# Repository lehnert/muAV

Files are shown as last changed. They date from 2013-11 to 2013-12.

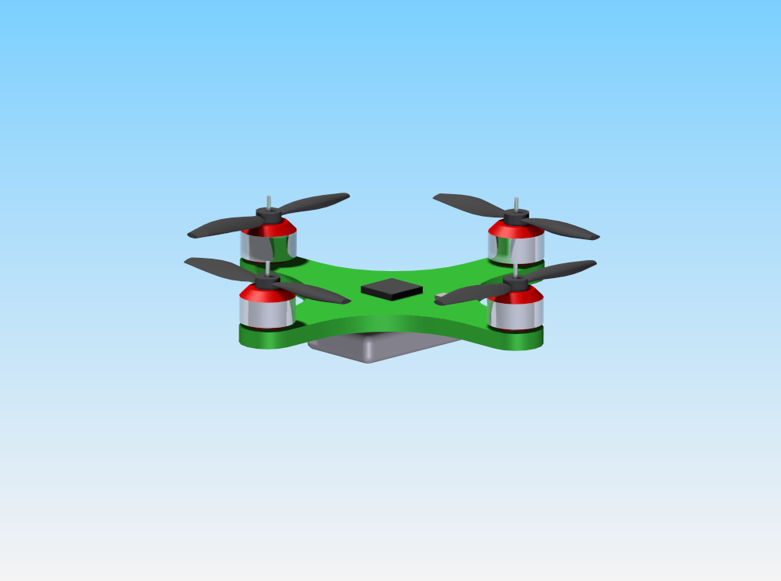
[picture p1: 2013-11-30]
Mechanial Design/images/quadrotor_image2.bmp

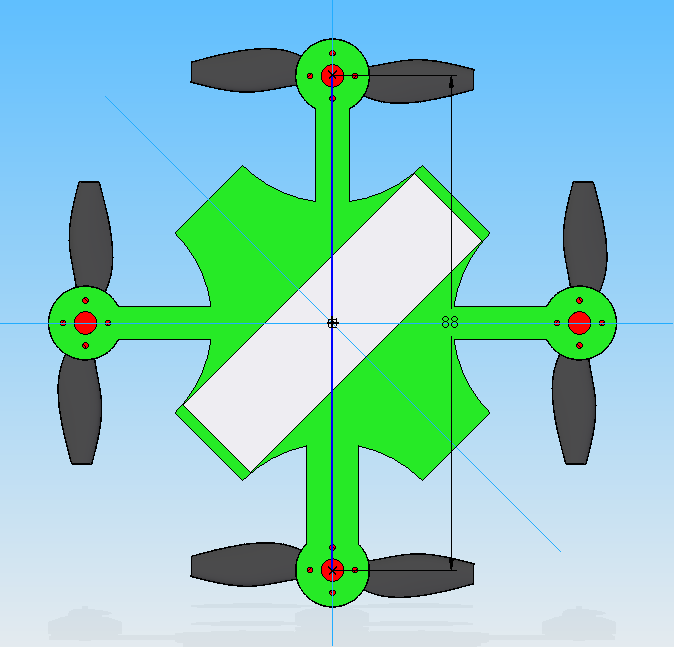
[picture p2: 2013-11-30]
Mechanial Design/images/quadrotor_image4_dimensions2.bmp

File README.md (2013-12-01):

µAV (muAV - Micro Unmanned Aerial Vehicle ) 
====

This project has been developed within the Cyphy Lab at the Queensland University of Technology. More information can be found at https://wiki.qut.edu.au/display/cyphy/Open+Source+Palm+Sized+Quadrotor

The aim of this project is to develop an open source micro unmanned aerial vehicle that is capable of autonomously nagivating within an indoor environment, which also fits in the palm of your hand. The concept has been designed to be cheap and easily constructed by using a single PCB board as the mechanical and electrical design of the system. An image of the final design is shown below.

Motivation:

The aim of the micro quadrotor project is to provide a lightweight (approximately 86g) and cheap robotic research platform that can be used for a range of robotic applications. One possible application could be a cheap test bed for robotic swarm research. This project was created to start an open source PCB only quadrotor for research applications. The idea was to create the simplest PCB only design in which all hardware is integrated. The hardware was selected to be state of the art allowing the system to be fully autonomous and used in high level research applications. Applications could include low cost robotic swarms or search and rescue in constrained environments.

Contributors:

Christophe Lehnert - https://wiki.qut.edu.au/display/cyphy/Chris+Lehnert
Peter Corke - https://wiki.qut.edu.au/display/cyphy/Peter+Corke

License:

 GNU GENERAL PUBLIC LICENSE  Version 3, 29 June 2007

 Copyright (C) 2007 Free Software Foundation, Inc. [http://fsf.org/]
 Everyone is permitted to copy and distribute verbatim copies
 of this license document, but changing it is not allowed.

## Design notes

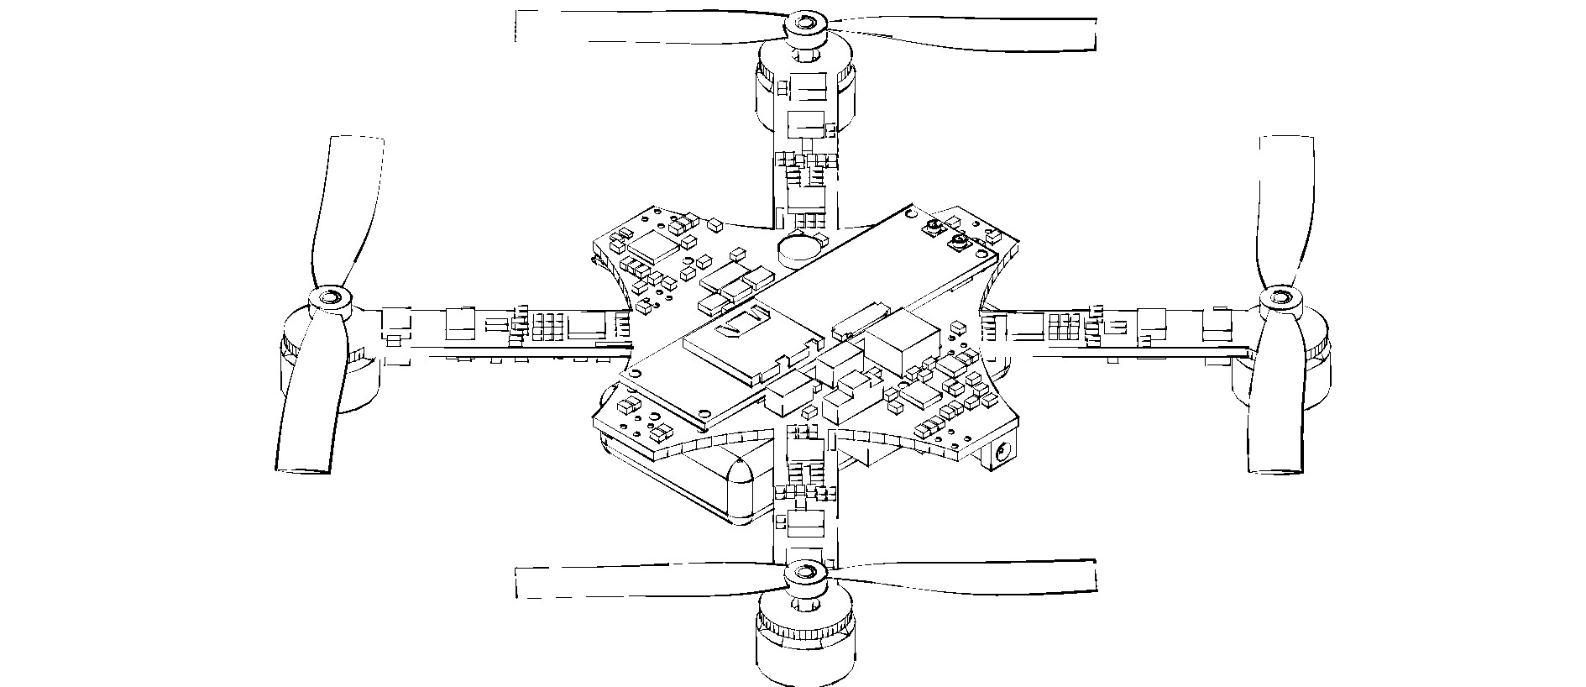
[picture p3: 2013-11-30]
Mechanial Design/images/quadrotor.jpg

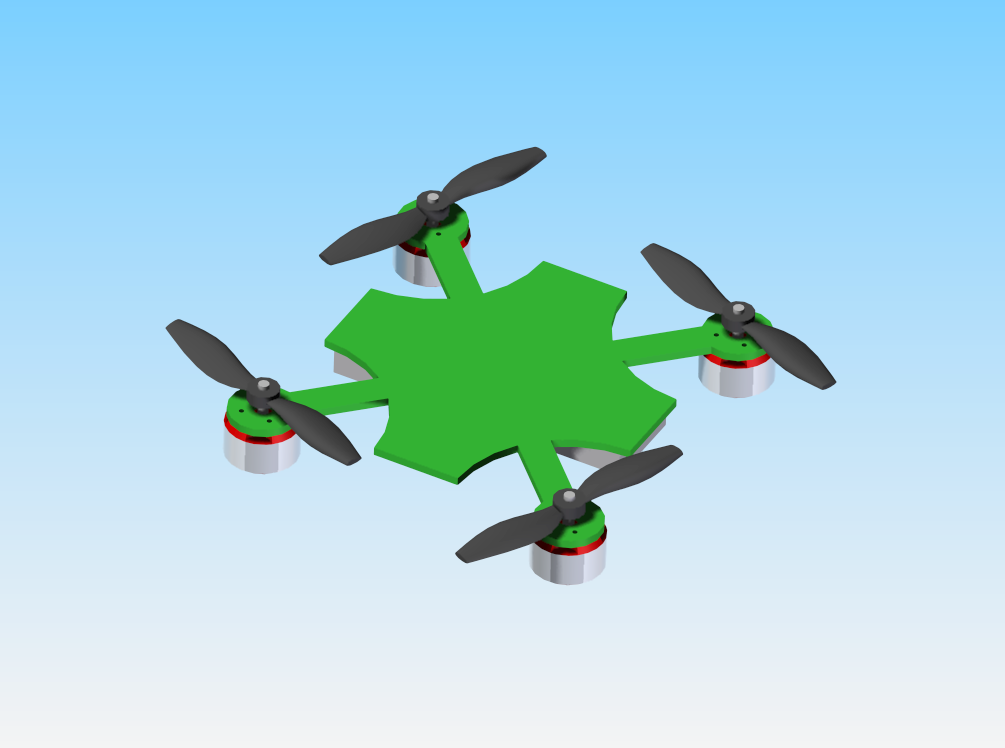
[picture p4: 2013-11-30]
Mechanial Design/images/new motor mounted.bmp

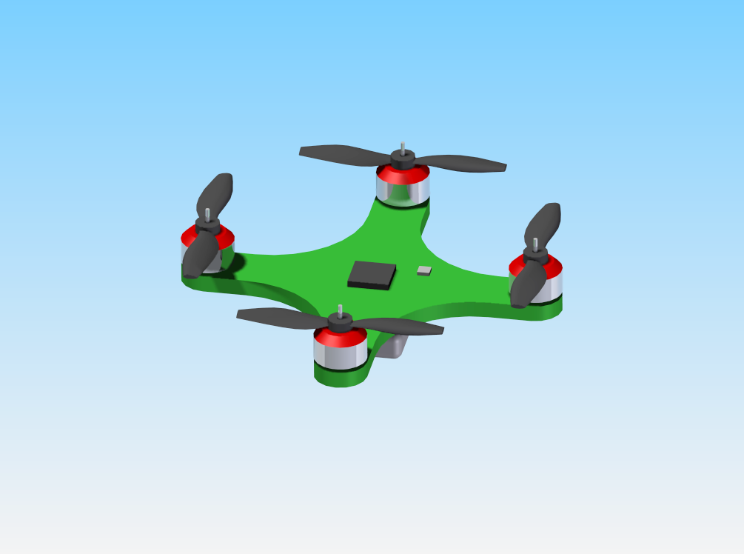
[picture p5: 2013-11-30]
Mechanial Design/images/quadrotor_image1.bmp

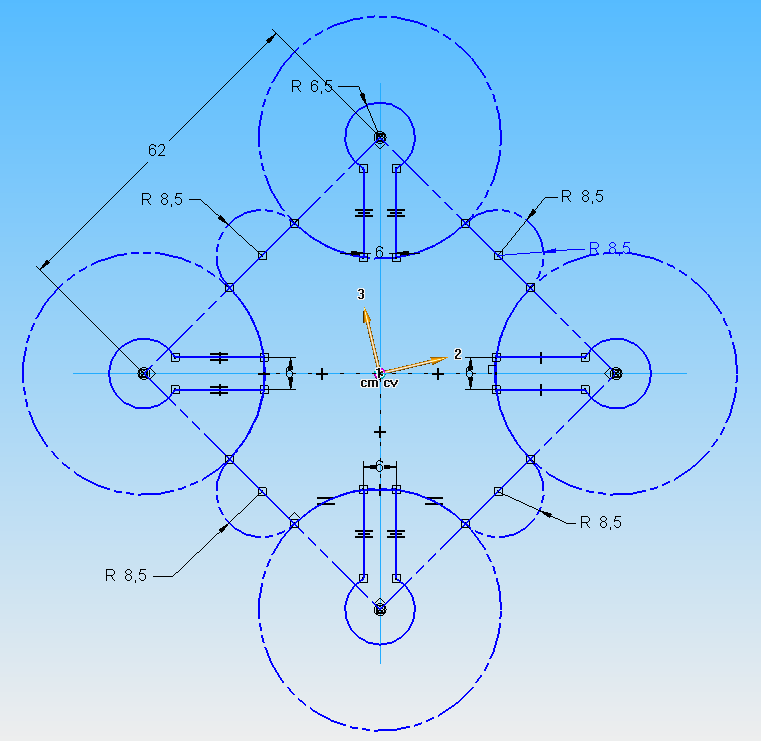
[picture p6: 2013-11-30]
Mechanial Design/images/quadrotor_image4_dimensions3.bmp

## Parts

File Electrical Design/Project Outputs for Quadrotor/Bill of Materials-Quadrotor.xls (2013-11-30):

Comment | Designator | Value | Footprint | Quantity | Manufacturer 1 | Supplier 1 | Supplier Order Qty 1 | Supplier Part Number 1 | Supplier Stock 1 | Supplier Subtotal 1 | Supplier Unit Price 1
HMC5843 | Mag1 |  | HMC5843 | 1 | Loading... | Sparkfun |  | COM-09441
SW-PB | SW1, SW2 |  | SM_SW | 2 | Loading... | Sparkfun |  | COM-08229
Triple axis gyroscope | IMU |  | QFN50P400X400X95-24N | 1 |  | Invensense
XTAL | XTAL |  | XTAL 16Mhz | 1 | Loading... | Farnell |  | 1640930
 | Rsns1 | 0.02 75PPM | CRA2512 | 1 | Bourns Inc. | Digi-Key | 1 | CRA2512-FZ-R020ELFCT-ND | 57343 | 0.49 | 0.49
3 axis accelerometer | ACCEL |  | 16 pin 3mmx3mm LGA | 1 | Analog Devices Inc | Digi-Key | 1 | ADXL345BCCZ-RLCT-ND | 12493 | 7.79 | 7.79
32Khz Oscillator | Osc2 |  | Oscillator | 1 | Abracon Corporation | Digi-Key | 1 | 535-9999-1-ND | 2117 | 5.06 | 5.06
ATmega8L-8AC | U1, uC1_E1, uC1_E2, uC1_E3, uC1_E4 |  | 32A_N | 5 | Atmel | Digi-Key | 5 | ATMEGA8L-8MU-ND, ATMEGA328-AU-ND
BC817-25 | Q1_E1, Q1_E2, Q1_E3, Q1_E4, Q2_E1, Q2_E2, Q2_E3, Q2_E4, Q3_E1, Q3_E2, Q3_E3, Q3_E4 |  | SOT-23 | 12 | NXP Semiconductors | Digi-Key | 12 | 568-1630-1-ND | 211012 | 2.59 | 0.22
BQ24103A | USBCHRG |  | QFN50P350X450X100-20N | 1 | Texas Instruments | Digi-Key | 1 | 296-22739-1-ND | 11380 | 6 | 6
Bq29312A | Bprot1 |  | TSOP65P640X120-24N | 1 | Texas Instruments | Digi-Key | 1 | 296-19870-1-ND | 874 | 3 | 3
CHOKE | FB2, FB3 |  | INDC1608L | 2 | Taiyo Yuden | Digi-Key | 2 | 587-1869-1-ND | 27225 | 0.66 | 0.33
Diode 10TQ035 | D14, D15 |  | DIODE | 2 | ON Semiconductor | Digi-Key | 2 | MBRS320T3GOSCT-ND | 17230 | 1.6 | 0.8
FDN-306P | Q4 |  | SOT-23 | 1 | Fairchild Semiconductor | Digi-Key | 1 | FDN306PCT-ND | 19874 | 0.55 | 0.55
IC_FT232RQ | FTDI |  | QFN-32 | 1 | FTDI, Future Technology Devices International Ltd | Digi-Key | 1 | 768-1067-2-ND | 0
Inductor | L1, L4 | 10uH, 15uH | INDM7575X45N | 2 | SUMIDA AMERICA COMPONENTS INC | Digi-Key | 2 | 308-1502-1-ND | 8486 | 2.84 | 1.42
MIC5427 | Reg1 |  | SOT23-STD-5-Lead | 1 | Micrel Inc | Digi-Key | 1 | 576-1288-1-ND | 10713 | 0.9 | 0.9
microUSB | mUSB1 |  | microUSB | 1 | Molex Inc | Digi-Key | 1 | WM17141CT-ND | 12801 | 1.31 | 1.31
MOSFET-N | Q8, Q10 |  | CSD16321Q5 | 2 | Texas Instruments | Digi-Key | 2 | 296-24517-1-ND | 9102 | 4.56 | 2.28
MOSFET-P | CHG1, DSG1, Q5, Q6, Q7 |  | CSD16321Q5_PFET | 5 | Texas Instruments | Digi-Key | 5 | 296-24260-1-ND | 14707 | 7.75 | 1.55
PWR2.5 | DC IN |  | DC Power JAck | 1 | CUI Inc | Digi-Key | 1 | CP1-022PJCT-ND | 3574 | 1.34 | 1.34
Rpull | Rsns2 | 0.1 | CRA2512 | 1 | Bourns Inc. | Digi-Key | 1 | CRA2512-FZ-R100ELFCT-ND | 33045 | 0.49 | 0.49
single tristate output line buffer | B1 |  | SOT95P280X145-5N | 1 | Texas Instruments | Digi-Key | 1 | 296-1115-1-ND | 12104 | 0.42 | 0.42
SW DPDT | S1 |  | SPDT | 1 | C&K Components | Digi-Key | 1 | 401-2002-1-ND | 14690 | 0.56 | 0.56
Switch mode regulator | 3.3PWR |  | TSOP65P640X120_HS-16N | 1 | Texas Instruments | Digi-Key | 1 | 296-22457-1-ND | 4016 | 10.34 | 10.34
T491A | C59 | 68uF | A | 1 | Kemet | Digi-Key | 1 | 399-4698-1-ND | 87013 | 0.88 | 0.88
T492C | C47_E1, C47_E2, C47_E3, C47_E4, C66 | 100uF | C | 5 | Kemet | Digi-Key | 5 | 399-5214-1-ND | 83455 | 6.7 | 1.34
Vtrans_2Bit | Vtrans1 |  | TSOP65P400X130-8N | 1 | Texas Instruments | Digi-Key | 1 | 296-17232-1-ND | 20290 | 0.84 | 0.84
 | C25, C61, C63, C64, C65 | 0.1uF, 10uF | 0603_CAP | 5
 | JP3, JP4, R52, R53, R54, R61, R62, R63 | 7.5K, 100 | 0603_RES | 8
 | R55, R56, R60 | 100K | RESC1608L | 3
2 Cell Battery | Battery |  | Turnigy Nanotech 2cell | 1
brushless motor | MTR1_E1, MTR1_E2, MTR1_E3, MTR1_E4 |  | Motor Combo | 4
Cap | C11, C12, C13, C14, C15, C16, C17, C18, C19, C20, C21, C22, C23 | 100nF, 100pF | 0603_CAP | 13
Cap Pol3 | C50, C52 | 1uF, 10uF | 0603_Cap | 2
Gumstix Overo Fire | GSTX1 |  | GUMSTIX | 1
Header 4 | P1, P2_E1, P2_E2, P2_E3, P2_E4 |  | PRG_HEADER | 5
JUMPER | JP1, JP2 |  | JUMPER | 2
LED0 | CHRG, DONE, LED1, LED2, LED_E1, LED_E2, LED_E3, LED_E4, PWR, PWR ON, RX1, TX1 |  | 0603_RES | 12
NP mosfet pair | NPA1_E1, NPA1_E2, NPA1_E3, NPA1_E4, NPB1_E1, NPB1_E2, NPB1_E3, NPB1_E4, NPC1_E1, NPC1_E2, NPC1_E3, NPC1_E4 |  | SOIC127P600-8L | 12
Rdrive | R6_E1, R6_E2, R6_E3, R6_E4, R11_E1, R11_E2, R11_E3, R11_E4 | 10K | 0603_RES | 8
Res Thermal | RT1 |  | RESC2012N | 1
Res1 | R27, R28, R29, R30, R31, R32, R33, R35, R36, R37, R38, R39, R40, R41, R42, R43, R44, R45, R46 | 1K | 0603_RES | 19
Res3 | R1, R2, R50, R51, R57, R58, R59 | 5.7K, 10K, 20K | 0603_RES | 7
Rpull | R3, R4_E1, R4_E2, R4_E3, R4_E4, R5_E1, R5_E2, R5_E3, R5_E4, R7_E1, R7_E2, R7_E3, R7_E4, R8_E1, R8_E2, R8_E3, R8_E4, R9_E1, R9_E2, R9_E3, R9_E4, R10_E1, R10_E2, R10_E3, R10_E4, R12_E1, R12_E2, R12_E3, R12_E4, R13_E1, R13_E2, R13_E3, R13_E4, R14_E1, R14_E2, R14_E3, R14_E4, R15_E1, R15_E2, R15_E3, R15_E4, R16_E1, R16_E2, R16_E3, R16_E4, R17_E1, R17_E2, R17_E3, R17_E4, R18_E1, R18_E2, R18_E3, R18_E4, R19_E1, R19_E2, R19_E3, R19_E4, R20_E1, R20_E2, R20_E3, R20_E4, R21_E1, R21_E2, R21_E3, R21_E4, R22_E1, R22_E2, R22_E3, R22_E4, R23_E1, R23_E2, R23_E3, R23_E4, R24_E1, R24_E2, R24_E3, R24_E4, R25_E1, R25_E2, R25_E3, R25_E4, R26_E1, R26_E2, R26_E3, R26_E4, R34_E1, R34_E2, R34_E3, R34_E4, R47, R48, R49, R64, R65, R66, R67_E1, R67_E2, R67_E3, R67_E4, R68_E1, R68_E2, R68_E3, R68_E4, R69_E1, R69_E2, R69_E3, R69_E4, R70_E1, R70_E2, R70_E3, R70_E4, R71, R72, R73, R74, R75, R76_E1, R76_E2, R76_E3, R76_E4, R77 | 1K, 4.7K, 8.2K, 9.31K, 10K, 16K, 33K, 100, 270, 442K | 0603_RES | 121
SCP1000-D11 | Prssr1 |  | SCP1000-D11 | 1
SDP8436 | SENS1, SENS2, SENS3, SENS4, SENS5, SENS6 |  | T-1SL | 6
SEP8736 | E1, E2, E3, E4, E5, E6 |  | T-1SL | 6
X7R Cap | C1, C2, C3, C4, C5, C6, C7, C8, C9, C10, C24, C26, C27, C28, C29, C30, C31, C32, C33, C34, C35, C36, C37, C38, C39, C40, C41, C42, C43, C44, C45_E1, C45_E2, C45_E3, C45_E4, C46, C48, C51, C53, C54, C55_E1, C55_E2, C55_E3, C55_E4, C56, C57, C58, C60, C62, Cesc1_E1, Cesc1_E2, Cesc1_E3, Cesc1_E4 | 0.1uF, 0.22uF, 0.47uF, 1uF, 2.2nF, 4.7uF, 10nF, 10uF | 0603_CAP | 52

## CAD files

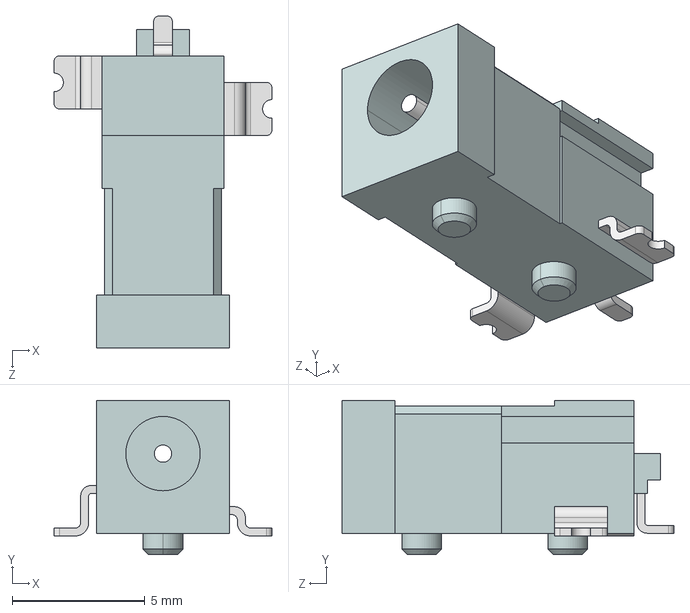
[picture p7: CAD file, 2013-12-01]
DataSheets/Other components/CUI-PJ1-022-SMT.step
8.20 x 5.80 x 12.5 mm

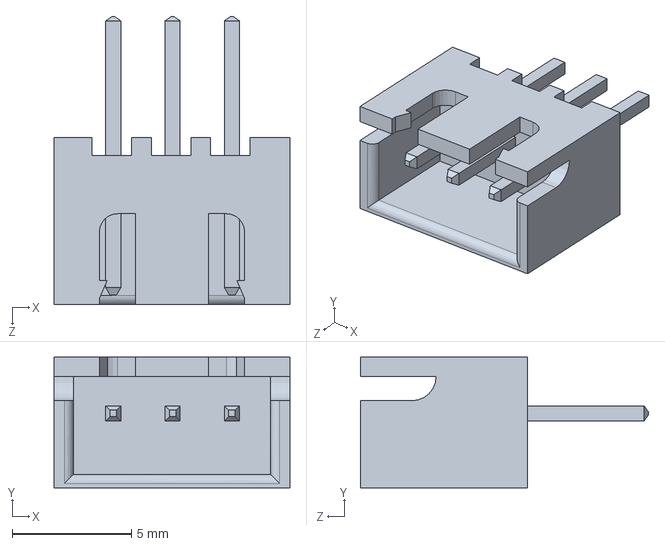
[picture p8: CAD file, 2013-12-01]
DataSheets/Other components/Part2.SLDPRT
9.91 x 5.49 x 12.1 mm

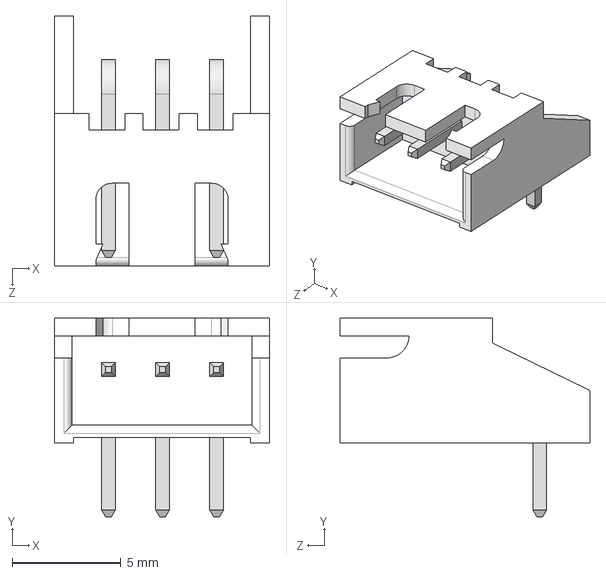
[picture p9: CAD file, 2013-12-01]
DataSheets/Other components/User Library-jst-xh-header-rangle.step
9.91 x 9.14 x 11.5 mm

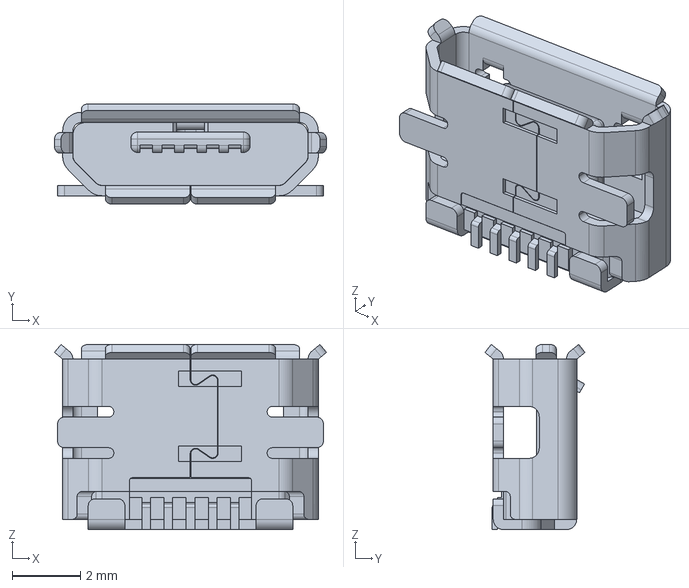
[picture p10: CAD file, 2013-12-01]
DataSheets/Other components/473460001.stp
7.98 x 2.94 x 5.43 mm

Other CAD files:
DataSheets/Other components/JST XH.STEP
DataSheets/Other components/User Library-jst-xh-header-rangle.SLDPRT

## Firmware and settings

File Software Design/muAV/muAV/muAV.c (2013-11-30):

/*
 * muAV.cpp
 *
 * Created: 18/12/2012 12:39:31 PM
 *  Author: n7574258
 */ 

#include "global.h"
#include "global_parameters.h"

#include <string.h>
#include <avr/io.h>
#include <avr/interrupt.h>

#include "imu3000.h"
#include "motorControl.h"
#include "control.h"
#include "uart.h"
#include "i2c.h"
#include "mavlink_functions.h"

void process_request(char myReceivedByte);
void sendIMUData(void);

volatile uint8_t global_counter;
volatile uint16_t raw_data_freq = 1;

volatile int32_t roll_desired = 0;
volatile int32_t pitch_desired = 0;
volatile int32_t yaw_desired = 0;
volatile int32_t thrust_desired = 0;



//MAVLINK Flags
volatile uint8_t MAVLINK_DATA_STREAM = FALSE;
volatile uint8_t MAVLINK_HEARTBEAT = FALSE;
volatile uint8_t MAVLINK_RECEIVE = FALSE;
volatile uint8_t SEND_STATUS = FALSE;

volatile uint64_t time_us = 0;

volatile IMU_t imu;

volatile state_t muav_state;

volatile uint8_t IMPLEMENT_STEP = FALSE;

int32_t manual_inputs[4] = {0,0,0,0};
	
volatile uint8_t step_speed = STEP_IDLE_SPEED;

int main(void)
{
	//muav_state = STOP;
	char myReceivedByte;
	
	uartInit();
	//uartSetBaudRate(57600);
	uartSetBaudRate(115200);
	
	//rprintfInit(uartSendByte);

	//Setup Motor control
	init_motors();
	
	i2cInit();
	i2cSetBitrate(400);
	
	// Initialise IMU
	init_imu();
	
	mavlink_init();
	
	//initalise parameters from eeprom
	read_param_from_eeprom();

	ENABLE_LED1;
	ENABLE_LED2;

	mavlink_set_mode(MAV_MODE_PREFLIGHT);
	mavlink_set_state(MAV_STATE_STANDBY);
	
	//init control loop
	initControlLoop();
	

	while(1){	
			
		communication_receive();
		
		if(MAVLINK_HEARTBEAT){
			MAVLINK_HEARTBEAT = FALSE;
			mavlink_send_heartbeat();
		}
		
		//if(SEND_STATUS){
		//	SEND_STATUS = FALSE;
		//	mavlink_send_status();
		//}		
				
		if(MAVLINK_RECEIVE){	
			param_queued_send(); // Send parameters at 10 Hz, if previously requested	
			MAVLINK_RECEIVE = FALSE;

		}else if(MAVLINK_DATA_STREAM ){
			data_stream_send();		
			MAVLINK_DATA_STREAM = FALSE;
		}

	
		/*if(uartReceiveByte(&myReceivedByte))
		{
			LED1_TOGGLE;
			if(myReceivedByte == 'R'){
				system_mode = MAV_MODE_STABILIZE_ARMED;		
				sendIMUData();
				
				//LED1_TOGGLE;
			}else if(myReceivedByte == 'P'){
				system_mode = MAV_MODE_STABILIZE_DISARMED;
				sendIMUData();
			}
			//process_request(myReceivedByte);	
		}*/		
	} 

	return 0;   
}


ISR(TIMER2_COMPA_vect)
{	
	static uint16_t heartbeat_counter = 0, param_counter = 0, status_counter = 0, data_counter, step_counter = 0;

	//global_counter = TCNT2;
	
		
	switch(system_mode)
	{
		case MAV_MODE_PREFLIGHT:
		{
			
			
		}
		break;
		
		case MAV_MODE_STABILIZE_DISARMED:
		{
			//LED1_OFF;
			read_imu(&imu);
			for(int i = 0; i < nMOTORS; i++) {
				writePWMduty(0, &(motors[i]));
			}
			//PDcontrol(0,0,0,35,&imu,FALSE);
			pitchPDcontrol(0, 35, &imu, FALSE);
		}
		break;
		
		case MAV_MODE_STABILIZE_ARMED:
		{
			//LED1_OFF;
			read_imu(&imu);
			//PDcontrol(0,0,0,35,&imu,TRUE);
			
			pitchPDcontrol(0, 35, &imu, TRUE);
			
			//writePWMduty((uint8_t)25, &(motors[0]));
			
			//rollPDcontrol(0, 30, &imu, TRUE);
			//pitchPDcontrol(pitch_desired, thrust_desired, &imu, &motor_power1, &motor_power2, FALSE);
			//yawPDcontrol(0, 35, &imu, TRUE);
			//yawPDcontrol(yaw_desired, thrust_desired, &imu, TRUE);
		}
		break;
		
		case MAV_MODE_MANUAL_ARMED:
		{
			
			const uint8_t MAX_INPUT = 160;
			const uint8_t MIN_INPUT = 0;
			
			manual_inputs[2] = thrust_desired + roll_desired + yaw_desired;
			manual_inputs[1] = thrust_desired - roll_desired + yaw_desired;
			
			manual_inputs[0] = thrust_desired + pitch_desired - yaw_desired;
			manual_inputs[3] = thrust_desired - pitch_desired - yaw_desired;
			

			for(int i = 0; i < nMOTORS; i++) {
				manual_inputs[i] = MAX(MIN(manual_inputs[i],MAX_INPUT),MIN_INPUT);
				writePWMduty((uint8_t)manual_inputs[i], &(motors[i]));
								
			}
			
			//read_imu(&imu);
			//manual_inputs[1] = MAX(MIN(manual_inputs[1],MAX_INPUT),MIN_INPUT);
			//writePWMduty((uint8_t)manual_inputs[1], &(motors[1]));

			
		
			/*if(step_counter < 250*STEP_PRETIME){
				writePWMduty(step_speed, &(motors[STEP_MOTOR]));
				step_counter++;
				
			}else if((step_counter >= 250*STEP_PRETIME) && (step_counter < 250*(STEP_PRETIME+STEP_TIME))){
				writePWMduty(step_speed, &(motors[STEP_MOTOR]));
				step_counter++;
				LED1_ON;
			}else{
				writePWMduty(0, &(motors[STEP_MOTOR]));
				LED1_OFF;
				if(step_speed < STEP_FINAL_SPEED){
					step_speed += STEP_SPEED_SIZE;
					step_counter = 250*STEP_PRETIME;
			    }else{
					step_speed += STEP_IDLE_SPEED;
					step_counter = 0;
				}								
				
			}*

			
			manual_inputs[0] = MAX(MIN(manual_inputs[0],MAX_INPUT),MIN_INPUT);
			manual_inputs[3] = MAX(MIN(manual_inputs[3],MAX_INPUT),MIN_INPUT);
			
			writePWMduty((uint8_t)manual_inputs[0], &(motors[0]));
			writePWMduty((uint8_t)manual_inputs[3], &(motors[3]));
			writePWMduty(0, &(motors[2]));
			writePWMduty(0, &(motors[1]));*/

					
		}
		break;
		
	
		
		//mode unknown stop motors
		default:
		{
			//for(int i = 0; i < nMOTORS; i++) {
			//	writePWMduty(0,&(motors[i]));
			//}
			
		}
		break;
		
		
	}
	
	
	
	//update counters
	heartbeat_counter++; param_counter++; status_counter++; data_counter++;
	
	//0.5Hz
	if(status_counter > 500){SEND_STATUS = TRUE; status_counter = 0;}
	//10Hz
	if(param_counter > 25){MAVLINK_RECEIVE = TRUE; param_counter = 0;}
	//1Hz		
	if(heartbeat_counter > 250){LED2_TOGGLE;MAVLINK_HEARTBEAT = TRUE; heartbeat_counter = 0;}
	//Varaible Freq
	if(m_data_stream_on){
		if(data_counter > 250/raw_data_freq){MAVLINK_DATA_STREAM = TRUE; data_counter = 0;	}
	}else{
		MAVLINK_DATA_STREAM = FALSE;
	}	
	//update time in microseconds (250Hz = 4000us per cycle)
	time_us+=4000;
	
	//global_counter = TCNT2 - global_counter;
	//uartSendByte(global_counter);
		
}


void sendIMUData(void)
{
	char *ptr = 0;
	uartAddToTxBuffer(0xAA);
	uartAddToTxBuffer(0xAA);
	
	/*ptr = (char *)&(motor_power1);
	uartAddToTxBuffer(ptr[0]);
	uartAddToTxBuffer(ptr[1]);
	uartAddToTxBuffer(ptr[2]);
	uartAddToTxBuffer(ptr[3]);
	
	ptr = (char *)&(motor_power2);
	uartAddToTxBuffer(ptr[0]);
	uartAddToTxBuffer(ptr[1]);
	uartAddToTxBuffer(ptr[2]);
	uartAddToTxBuffer(ptr[3]);*/
	
	/*ptr = (char *)&(imu.raw_accel_x
	uartAddToTxBuffer(ptr[0]);
	uartAddToTxBuffer(ptr[1]);

	ptr = (char *)&(imu.gyro_y);
	uartAddToTxBuffer(ptr[0]);
	uartAddToTxBuffer(ptr[1]);*/


	/*ptr = (char *)&(imu.accel_x);
	uartAddToTxBuffer(ptr[0]);
	uartAddToTxBuffer(ptr[1]);

	ptr = (char *)&(imu.accel_y);
	uartAddToTxBuffer(ptr[0]);
	uartAddToTxBuffer(ptr[1]);*/

	ptr = (char *)&(imu.roll);
	uartAddToTxBuffer(ptr[0]);
	uartAddToTxBuffer(ptr[1]);
	uartAddToTxBuffer(ptr[2]);
	uartAddToTxBuffer(ptr[3]);
	
	ptr = (char *)&(imu.pitch);
	uartAddToTxBuffer(ptr[0]);
	uartAddToTxBuffer(ptr[1]);
	uartAddToTxBuffer(ptr[2]);
	uartAddToTxBuffer(ptr[3]);

	/*ptr = (char *)&(imu.pitch);
	uartAddToTxBuffer(ptr[0]);
	uartAddToTxBuffer(ptr[1]);
	uartAddToTxBuffer(ptr[2]);
	uartAddToTxBuffer(ptr[3]);*/
		
	uartSendTxBuffer();
}

void process_request(char myReceivedByte){

	if(myReceivedByte == SPIN_UP)
	{
		muav_state = IDLE;
	}
	
	if(myReceivedByte == START_CONTROL)
	{
		muav_state = START;
	}
	
	if(myReceivedByte == PAUSE)
	{
		muav_state = STOP;
	}
	
	if(myReceivedByte == CALIBRATE)
	{
		LED1_TOGGLE;
		calibrate_motors();
	}
	
	if(myReceivedByte == RESET_MOTORS)
	{
		reset_motors();
	}



	if(myReceivedByte == ROLL_LEFT){
		writePWMduty(motors[0].duty+ROLL_DELTA,&(motors[0]));
		
		if((int8_t)motors[2].duty-ROLL_DELTA < 0)
		{
			writePWMduty(0,&(motors[2]));
		}else{
			writePWMduty(motors[2].duty-ROLL_DELTA,&(motors[2]));
		}
	}
	
	if(myReceivedByte == ROLL_RIGHT){
		if((int8_t)motors[0].duty-ROLL_DELTA < 0)
		{
			writePWMduty(0,&(motors[0]));
		}else{
			writePWMduty(motors[0].duty-ROLL_DELTA,&(motors[0]));
		}
		writePWMduty(motors[2].duty+ROLL_DELTA,&(motors[2]));
	}
	
	if(myReceivedByte == PITCH_UP){
		writePWMduty(motors[1].duty+PITCH_DELTA,&(motors[1]));
		if(motors[3].duty < 0)
		{
			writePWMduty(0,&(motors[3]));
		}else{
			writePWMduty(motors[3].duty-ROLL_DELTA,&(motors[3]));
		}
	}
	
	if(myReceivedByte == PITCH_DOWN){
		if(motors[1].duty < ROLL_DELTA)
		{
			writePWMduty(0,&(motors[1]));
		}else{
			writePWMduty(motors[1].duty-ROLL_DELTA,&(motors[1]));
		}
		writePWMduty(motors[3].duty+PITCH_DELTA,&(motors[3]));
	}
		

	
	if(myReceivedByte == MOTOR_UP_1)
	{
		writePWMduty(motors[0].duty + UP_DELTA,&(motors[0]));
		
		/*for(int i = 0; i < nMOTORS; i++) {
			writePWMduty(motors[i].duty + 100,&(motors[i]));
		}*/
	}
	
	if(myReceivedByte == MOTOR_UP_2)
	{
		writePWMduty(motors[1].duty + UP_DELTA,&(motors[1]));
	}
	if(myReceivedByte == MOTOR_UP_3)
	{
		writePWMduty(motors[2].duty + UP_DELTA,&(motors[2]));
	}
	if(myReceivedByte == MOTOR_UP_4)
	{
		writePWMduty(motors[3].duty + UP_DELTA,&(motors[3]));
	}
	
	if(myReceivedByte == MOTOR_DOWN_1)
	{
		writePWMduty(motors[0].duty < DOWN_DELTA ? 0 : (motors[0].duty - DOWN_DELTA),&(motors[0]));
	}
	
	if(myReceivedByte == MOTOR_DOWN_2)
	{
		writePWMduty(motors[1].duty < DOWN_DELTA ? 0 : (motors[1].duty - DOWN_DELTA),&(motors[1]));
	}
	
	if(myReceivedByte == MOTOR_DOWN_3)
	{
		writePWMduty(motors[2].duty < DOWN_DELTA ? 0 : (motors[2].duty - DOWN_DELTA),&(motors[2]));
	}
	if(myReceivedByte == MOTOR_DOWN_4)
	{
		writePWMduty(motors[3].duty < DOWN_DELTA ? 0 : (motors[3].duty - DOWN_DELTA),&(motors[3]));
	}
	
	/*if(myReceivedByte == MOTOR_DOWN)
	{
		for(int i = 0; i < nMOTORS; i++) {
			if(motors[i].duty > 0)
			writePWMduty(motors[i].duty - 1,&(motors[i]));
		}
	}*/
	

	
	
		
	
}

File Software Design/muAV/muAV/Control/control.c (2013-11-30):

/*
 * control.c
 *
 * Created: 1/07/2013 10:16:10 AM
 *  Author: Chris
 */ 
#include "control.h"
#include "motorControl.h"
#include "imu3000.h"
#include "global.h"
#include "global_parameters.h"
#include "eeprom_param.h"

#include <avr/interrupt.h>

#define MAX_ROLL_SPEED 60
#define MAX_PITCH_SPEED 60
#define MAX_YAW_SPEED 60
#define MIN_SPEED IDLE_SPEED

volatile int32_t m1_power, m2_power, m3_power, m4_power;
volatile int32_t power_difference_yaw, power_difference_roll, power_difference_pitch;

void initControlLoop()
{
	// initialize timer 2
	TCNT2 = 0;								// reset TCNT2
	//sbi(TIMSK2, TOIE2);						// enable TCNT2 overflow
	TCCR2A |= (1 << WGM21) | (0 << WGM20);
	
	TCCR2B |= (0 << WGM22) | (1 << CS22) | (1 << CS21) | (0 << CS20);
	TIMSK2 |= (1 << OCIE2A);
		
	//249 = 250Hz for 256 prescale	
	//249 = 500Hz for 128 prescale
	//155 = 800Hz for 128 prescale
	//249 = 1Khz for 64 prescale
	OCR2A = 249; 
	sei();
}

inline void rollPDcontrol(int32_t desired_roll, int32_t base_speed, volatile IMU_t *imu, uint8_t armed)
{
	//PD scaling factors
	//Gains defined in global.h 

	int32_t Kp_num = (int32_t)volatile_param_array.param[PID_ROLL_P];
	int32_t Kd_num = (int32_t)volatile_param_array.param[PID_ROLL_D];
	const int32_t K_den = 60000;//12;
	int32_t proportional = 0;
	int32_t derivative = 0;
	int32_t power_difference = 0;
	
	derivative = -imu->gyro_x;
	proportional = desired_roll - imu->roll;
	
	power_difference = (Kp_num*proportional/K_den)  +  (Kd_num*derivative/K_den);
	power_difference_roll = power_difference;

	// Compute the actual motor settings.  We never set either motor
	// to a negative value.
	if(power_difference > 0)
	{
		//+ form
		m3_power = MIN(base_speed + power_difference,MAX_ROLL_SPEED);
		m2_power = MAX(base_speed - power_difference,MIN_SPEED);
				
		//only apply power if motors are armed
		if(armed){
			writePWMduty((uint8_t)m3_power,&(motors[2]));
			writePWMduty((uint8_t)m2_power,&(motors[1]));
		}else{
			writePWMduty(0,&(motors[2]));
			writePWMduty(0,&(motors[1]));
		}				
					
	}else{
		//+ form
		m3_power = MAX(base_speed + power_difference,MIN_SPEED);
		m2_power = MIN(base_speed - power_difference,MAX_ROLL_SPEED);
		
		//only apply power if motors are armed
		if(armed){
			writePWMduty((uint8_t)m3_power,&(motors[2]));
			writePWMduty((uint8_t)m2_power,&(motors[1]));
		}else{
			writePWMduty(0,&(motors[2]));
			writePWMduty(0,&(motors[1]));
			
			
		}		
	}	
	
}

inline void pitchPDcontrol(int32_t desired_pitch, int32_t base_speed, volatile IMU_t *imu, uint8_t armed)
{
	//PD scaling factors
	//Gains defined in global.h
	int32_t Kp_num = (int32_t)volatile_param_array.param[PID_PITCH_P];
	int32_t Kd_num = (int32_t)volatile_param_array.param[PID_PITCH_D];
	const int32_t K_den = 60000;//12;
	
	int32_t proportional = 0;
	int32_t derivative = 0;
	
	int32_t power_difference = 0;

	derivative = -imu->gyro_y;
	proportional = desired_pitch - imu->pitch;
	power_difference = (Kp_num*proportional/K_den) +  (Kd_num*derivative/K_den);
    power_difference_pitch = power_difference;
	
	// Compute the actual motor settings.  We never set either motor
	// to a negative value.
	if(power_difference > 0)
	{
		m1_power = MIN(base_speed + power_difference,MAX_PITCH_SPEED);
		m4_power = MAX(base_speed - power_difference,MIN_SPEED);
		
		//+ form
		if(armed){
			writePWMduty((uint8_t)m1_power,&(motors[0]));
			writePWMduty((uint8_t)m4_power,&(motors[3]));
		}else{
			writePWMduty(0,&(motors[0]));
			writePWMduty(0,&(motors[3]));
		}			
	}else{
		m1_power = MAX(base_speed + power_difference,MIN_SPEED);
		m4_power = MIN(base_speed - power_difference,MAX_PITCH_SPEED);
		
		//+ form
		if(armed){
			writePWMduty((uint8_t)m1_power,&(motors[0]));
			writePWMduty((uint8_t)m4_power,&(motors[3]));
		}else{
			writePWMduty(0,&(motors[0]));
			writePWMduty(0,&(motors[3]));
		}			
	}
}

inline void PDcontrol(int32_t desired_yaw, int32_t desired_pitch, int32_t desired_roll, int32_t base_speed, volatile IMU_t *imu, uint8_t armed)
{
	//PD scaling factors
	//Gains defined in global.h
	int32_t Kp_num = (int32_t)volatile_param_array.param[PID_YAW_P];
	int32_t Kd_num = (int32_t)volatile_param_array.param[PID_YAW_D];
	
	const int32_t K_den = 60000;
	
	int32_t proportional = 0;
	int32_t derivative = 0;
	int32_t power_difference = 0;
	int32_t base_speed_pitch = 0, base_speed_roll = 0;

	derivative = -imu->gyro_z;
	
	proportional = desired_yaw - imu->yaw;

	power_difference = (Kp_num*proportional/K_den) +  (Kd_num*derivative/K_den);
	power_difference_yaw = power_difference;

	// Compute the actual motor settings.  We never set either motor
	// to a negative value.
	if(power_difference > 0)
	{
		//+ form
		base_speed_pitch = MAX(base_speed - power_difference,MIN_SPEED);
		base_speed_roll =  MIN(base_speed + power_difference,MAX_YAW_SPEED);		
	}else{
		base_speed_pitch = MIN(base_speed - power_difference,MAX_YAW_SPEED);			
		base_speed_roll = MAX(base_speed + power_difference,MIN_SPEED);
	}
	
	//use yaw base speeds as set point for roll and pitch base speeds
	rollPDcontrol(desired_roll, base_speed_roll, imu, armed);
	pitchPDcontrol(desired_pitch, base_speed_pitch, imu, armed);
}
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

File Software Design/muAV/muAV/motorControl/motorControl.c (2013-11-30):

#include "motorControl.h"
#include "global.h"
#include <util/delay.h>
#include <avr/interrupt.h>
#include <avr/io.h>



void init_motors()
{
	
	//setup reset line
	SET_DDR_PIN_OUTPUT(DDRB, PIN0);
	//set motor output pins
	DDRB |= (1<<PINB1)|(1<<PINB2);
	DDRD |= (1<<PIND5)|(1<<PIND6);
		
	configure_motor(&(motors[0]),0,PORTB,PINB1,M1_IDLE_SPEED, M1_OFFSET);
	configure_motor(&(motors[1]),1,PORTB,PINB2,M2_IDLE_SPEED, M2_OFFSET);
	configure_motor(&(motors[2]),2,PORTD,PIND5,M3_IDLE_SPEED, M3_OFFSET);
	configure_motor(&(motors[3]),3,PORTD,PIND6,M4_IDLE_SPEED, M4_OFFSET);
		
	initPWM();	
		
	calibrate_motors();	
		//reset motors
	//MOTORS_OFF;
	
	//Reset the RC pulse to zero to simulate throttle low position
	/*for(int i = 0; i < nMOTORS; i++) {
		//writeVelocity(0,&(motors[i]));
		writePWMduty(0,&(motors[i]));
	}*/
	//writePWMduty(0,&(motors[1]));
	//_delay_ms(50);
	//MOTORS_ON;
	
	
}

void configure_motor(volatile BLMOTOR_t *motor, uint8_t channel, uint8_t outputPort, uint8_t outputPin, uint8_t idle_speed, uint8_t pwmOffset)
{
	motor->channel = channel;
	motor->Port = outputPort;
	motor->Pin = outputPin;
	motor->idle_speed = idle_speed;
	motor->trim = pwmOffset;
	motor->duty = 0;
}	

// The motors can only be calibrated directly after the ESC's have been
// reset otherwise it will put full power to the motors
void calibrate_motors(void){
	
	//turn of control loop interrupt
	DISABLE_CONTROL_LOOP;
	
	//reset motors
	MOTORS_OFF;
	
	//Hold the RC pulse high to simulate high throttle position
	for(int i = 0; i < nMOTORS; i++) {
		//writeVelocity(255,&(motors[i]));
		writePWMduty(MAX_DUTY,&(motors[i]));
	}
	
	_delay_ms(50);
	//turn on motors while high throttle
	MOTORS_ON;
	//wait till the ESC's register high throttle calibration
	_delay_ms(1000);
	
	//Reset the RC pulse to zero to simulate throttle low position
	for(int i = 0; i < nMOTORS; i++) {
		//writeVelocity(0,&(motors[i]));
		writePWMduty(0,&(motors[i]));
	}
	//wait till the ESC's register low throttle calibration
	_delay_ms(1000);
	
	//turn of control loop interrupt
	ENABLE_CONTROL_LOOP;
	
}

void reset_motors(void){
	MOTORS_OFF;
	_delay_ms(100);
	MOTORS_ON;	
}

void start_motors(void)
{
	for(int i = 0; i < nMOTORS; i++) {
		writePWMduty(motors[i].idle_speed,&(motors[i]));
	}
}

void initPWM(void){
	
	//setup PWM timers 0 and 1
	TCNT1 = 0;

	
	//init PWM Duty to 0 (1ms)
	for(int i = 0; i < nMOTORS; i++) {
		writePWMduty(0, &(motors[i]));
	}		
	
	//setup PWM timers 0 and 1
	TCNT0 = 0;
	TCNT1 = 0;
	
	//Timer 0 mode = PWM Phase Correct 8bit mode (non inverted) 32 prescaler
	TCCR0A |= (1 << COM0A1) | (0 << COM0A0) | (1 << COM0B1) | (0 << COM0B0)  | (0 << WGM01) | (1 << WGM00);
	TCCR0B |= (0 << WGM02) | (0 << CS02) | (1 << CS01) | (1 << CS00);
	
	//Timer 1 mode = PWM Phase Correct 8bit mode (non inverted) 32 prescaler
	TCCR1A |= (1 << COM1A1) | (0 << COM1A0) | (1 << COM1B1) | (0 << COM1B0)  | (0 << WGM11) | (1 << WGM10);
	TCCR1B |= (0 << WGM13) | (0 << WGM12) | (0 << CS12) | (1 << CS11) | (01 << CS10);
	
	//init PWM output
	for(int i = 0; i < nMOTORS; i++) writePWMduty(0, &(motors[i]));
	sei();

}

void writePWMduty(uint8_t duty, volatile BLMOTOR_t *motor){
	
	motor->duty = duty;
	
	//scale duty from 0-255 to PWM ticks
	duty = (uint8_t)((uint16_t)duty*(MAX_DUTY_TICKS-MIN_DUTY_TICKS)/MAX_DUTY)+MIN_DUTY_TICKS;
	
	//bind limits
	duty = MAX(duty, MIN_DUTY_TICKS);
	duty = MIN(duty, MAX_DUTY_TICKS);
	
	switch (motor->channel)
	{
		case 0: //PINB2
			OCR1B = duty;
			break;
		case 1: //PINB1
			OCR1A = duty;
			break;
		case 2: //PIND5
			OCR0B = duty;
			break;
		case 3: //PIND6
			OCR0A = duty;
			break;
	}
}

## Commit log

2013-11-30 First commit of electrical design
    [Battery Pack & Charger.SchDoc, Bill of Materials-Quadrotor.xls, Bill of Materials-Quadrotor_edited.xls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]
2013-11-30 First commit of mechanical design
    [45mm_Quadrotor.cfg, 76mm_Quadrotor.cfg, pop adapter.cfg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]
2013-12-01 first commit of datasheets and documents
    [473460001.stp, CUI-PJ1-022-SMT.step, JST XH.STEP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]
2014-04-10 Added AVRlib to muAV software package
    [TcfTransactionLog.csv]
